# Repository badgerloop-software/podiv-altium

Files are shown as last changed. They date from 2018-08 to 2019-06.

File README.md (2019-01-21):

# podiv-altium
Altium repository for podiv. This project is set up to provide all documentation, design and data validation required for the Badgerloop Pod 4 PCBs.

## Prerequisites
Altium only works on Windows. See  [Altium System Requirements](https://www.altium.com/documentation/18.0/display/ADES/Altium+Designer+-+((System+Requirements))") for more information. An internet connection is required to connect to the license server and dual monitors are nice to ahve. Microsoft Excel is required for BOM generation.

## Installation
1. Contact Ethan Link or Ryan Castle to be added to the Badgerloop Team AltiumLive Account and the Badgerloop [Github](https://github.com/badgerloop-software"). You will receive an email from Altium with your account information. You may continue to step to step 8 without requiring an active license. If there is a delay for some reason, you can work on Altium training and practice on CAE computers or through [Citrix](https://remote.engr.wisc.edu/vpn/index.html), but we are usually able to add new users within 24 hours. CAE currently runs Altium 16, which has similar features but has a different interface and some bugs. Badgerloop currently supports Altium 19.0.10. 
2. Download the latest version of [Altium Designer](https://www.altium.com/products/downloads) 
3. Install Altium. Default file paths will work.
4. Insall [Git Bash](https://gitforwindows.org/") Git Bash (or whatever BASH emulation tool you are comfortable with)
5. Open Git Bash
6. Type the following commands into the command prompt window:
   + cd ../..
   + mkdir git
   + cd git
   + git clone https://github.com/badgerloop-software/podiv-altium.git
   + cd podiv-altium
   + git checkout -b <your-username_training>
   + Open Altium and sign in. You are now on a training branch that you will complete your first getting started project on if you are new to Altium. 
7. Go to User (Silhouette in the top right corner) -> License Management. Then Click Sign In and enter your username and password associated with Altium Live and accept the warning. It's also a good idea to check Sign me in when I start Altium Designer if you'd like to save a little time.

_NOTE: If you go click "Sign In" directly from User, you will be asked for a server address. This is not what you want. Go back to step 7 and hit License Management instead of Sign In._ 

8. Click Use to claim a license. If you are not using a valid license, you will be able to view files in Altium Designer but you will not be able to make edits. Ensure that you are choosing an Altium Designer License and not our PDN License. That's something else. 
9. You are now ready to use Altium. See [Training](#training) for more details on how to get started. 

## Training

+ View the [Badgerloop Altium Presentation](https://uwmadison.box.com/s/2sdt8kfaeyde04sg8edn62u7vtrdsiyx") for a getting started project. You can work locally for this project. Git-specific training will be posted at a later date. 
+ If you are new to using Git, read through the [Altium Git Guide](https://uwmadison.app.box.com/file/324684243638) which provides some common commands to get you started. 

## General Tips
+ Do not try to use Altium's built in check-out/commit tools. Instead, use Git from the terminal to perform git operations. This prevents a lot of conflicts. Learning how to use the command line is a really good thing to learn how to do as it's used in industry all over.
+ To save, CTRL + S may not save all of the files you are expecting it to. Instead, right click on the file you want to save and hit "save". Also, note that if a schematic document is edited, saving the entire project will only save the project structure, not the actual schematic file you have changed. 
+ Multiple libraries are used in part to reduce the number of conflicts between branches. It's important that you are regularly commiting and pushing your changes when multilpe users are working. Conflicts are possible to solve, but are somewhat challenging to do so. Libraries will be managed by Ryan Castle. Do not edit source libraries, instead, make changes in a temporary library.
+ Note that multilpe projects can reference the same libraries. Be careful if you are editing a component that has already been placed in another project, as even minor changes like pad size can have major unintended results. 

## Contributing
There are several ways to contribute to the repo. Check open issues to see what needs active work. Talk to the Avionics Lead or the Electrical Director about where your skill level can be most used.
+ Library components [TODO](https://github.com/badgerloop-software/podiv-altium/issues/16):

   + Schematic: Schematic libraries consist of the symbols used in schematics, as well as their pinoutsand link PCB and 3D components
   + PCB: PCB libraries consist of the footprints, pinouts and links to schematic symbols and 3D components. Footprints are the arrangement of pads and/or plated through-holes to physically attach and electrically connect a component to a printed circuit board. A silkscreen, keepout zone, and mechanical connections may also be added to a footprint
   + 3D Library: Each PCB footprint can be associated with a 3D STEP model and viewed in 3D mode of the PCB viewer. This is not required, but useful for exporting to the main pod MCAD as well as for enclosure design. 
+ Schematics:
   + Break out your datasheets! This is where the rubber meets the road of electrical engineering. Schematic design is where the highest level electrical engineering occurs, connecting different discrete components like resistors, capacitors, inductors and diodes to integrated circuits (ICs), connectors, hardware, etc. 
   + Schematic review: Look through an existing schematic and fill out the (still TODO) Schematic Review checklist. We want to catch issues as early as possible and correct before the board goes to layout or even worse, fabrication! 
+ PCBs:
   + I like to think of PCB layout as running through a maze several dozen times, where you control how the walls are constructed, there more more walls as you go along, and things can move as you go. PCB design is a learned skill, so the best thing to do is practice!
   + PCB review: Similar to schematic review, we want to find PCB layout issues before we send out to fabrication. Something as simple as a component flipped around can cause a boards unusable! 

## Directory Structure
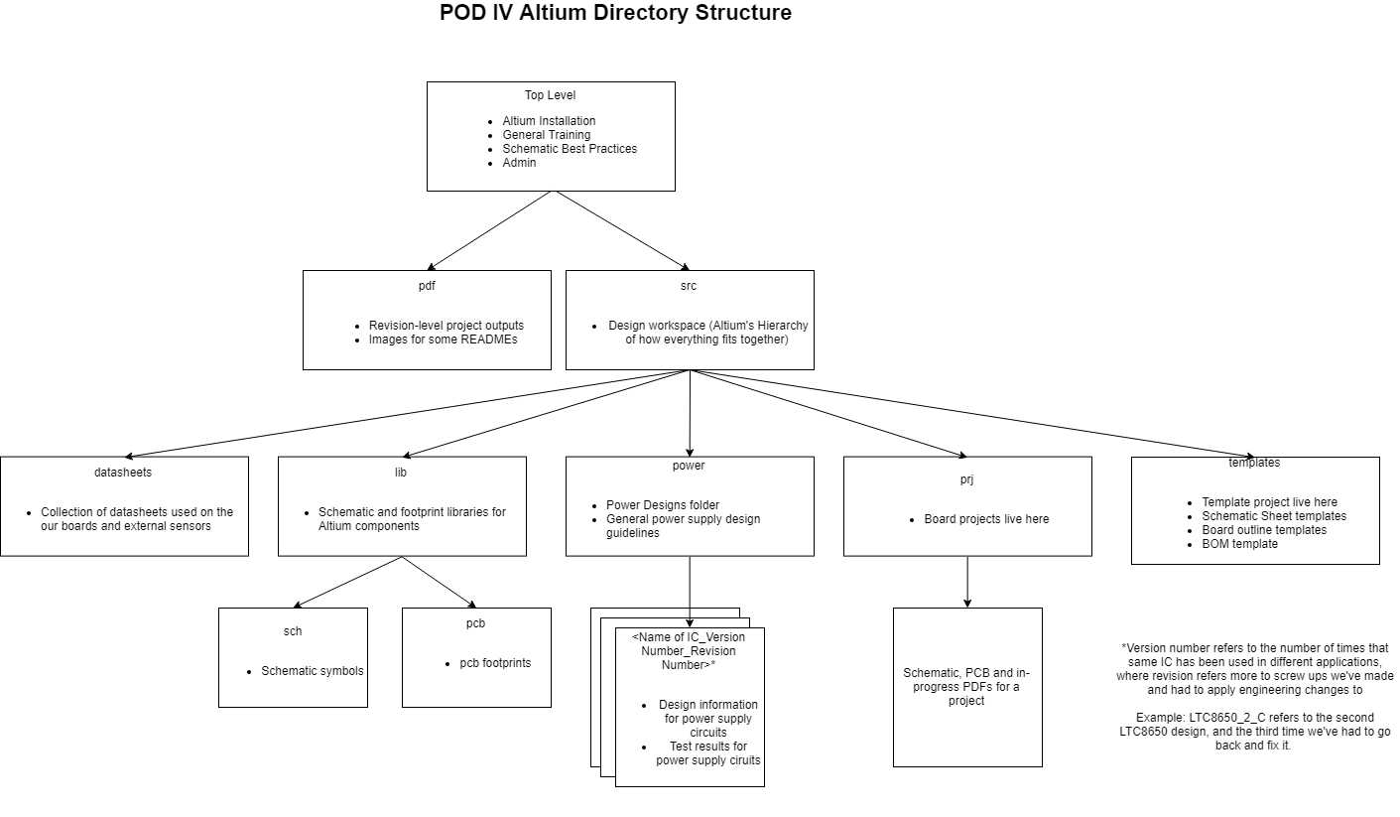
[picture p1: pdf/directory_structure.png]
Directory_Structure Directory Structure


## Contributors
+ [Ryan Castle](https://www.linkedin.com/in/ryan-castle-589721106/)
+ [Vaughn Kottler](https://www.linkedin.com/in/vaughnkottler/)
+ [Austin Muschott](https://www.linkedin.com/in/austin-muschott/)
+ [Tristan Steiner](https://www.linkedin.com/in/tristan-steiner-0bba76106/)

(Add yourself when you make your first commit!)

## Acknowledgements
+ [Altium](www.altium.com), for being an amazing sponsor! 
+ Dave Jones of the EEVBlog, as we'd have no idea what we were doing without his videos.

## Questions
If you have any questions, feel free to contact any contributor listed above on Slack (Badgerloop internal) or Linkedin (external)

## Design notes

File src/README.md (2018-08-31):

# Pod IV Multi-board PCB Project
The general approached for PCBs for Pod IV is to divide the workload into two types of boards-- processor boards and IO (Input/Output) boards. One processor board and one IO board will make up a module. The primary benefit to this approach is that the more complicated power and microcontroller circuitry can be done one time on the processor board, while module specific IO can be created to fit the specific module needs. 

## Module Notes:
+ Standard [connector](https://www.avnet.com/shop/emea/products/samtec/et60t-00-00-04-l-rt1-gp-3074457345629068722/") and pinout for each module allows for IO modules to be connected to any processor board safely
+ The blade connectors will be able to transfer the required current for up to 20 solenoids.
+ Must verify that signals routed over the longer leads are routed properly
+ Direct board <--> harness connection to eliminate module-box level wiring
+ I2C IO expanders used regularly as the standard interface between processor and IO boards. SPI and UART connections also routed to the connector but a NC (no connect) is acceptable.
+ 3D printed module boxes to fit the box to the boards, have holes pre-drilled

## Processor Board Notes:
+ 24V Input --> 5V, 3.3V outputs with reverse polarity protection, hold-up, surge stopper
+ Board mount processor with a QFN32 package utilized

## Module Board Notes:
+ Good project for beginners after you have completed the training board. 
+ Propoposed board ideas:
   + Navigation -- Accelerometer, Retroreflective sensor, distance sensor, wheel encoder
   + Pressure Vessel / Precharge PCB -- Pressure vessel monitoring and high voltage pre-charge circuit
   + Wireless communications -- replacement for the network access panel (NAP)
   + Braking -- IO for solenoids, pressure sensors
   + Low Voltage battery monitoring -- Battery management system for the low voltage system
   + Control Panel Display board -- Provide visual feedback for the system, useful for debugging.

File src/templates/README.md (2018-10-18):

# Templates
The purpose of this folder is to provide all templates for schematics sheets, PCBs, BOM, circuit snippets and reviews

## Circuit Snippets
[Badgerloop Altium Part II -- How to add a circuit snippet](https://www.youtube.com/watch?v=RExZlAXOayE&t=1s)

## Reviews
There are two templates associated with a review, the word document format and a powerpoint. The nominal workflow for a schematic or layout review are as follows:
1. The designer will output the following files and commit them to their working branch:
     * Schematic PDF
     * Board layout drawings, broken out layer by layer 
     * Gerbers, Drill Drawings
     * Pick and Place Files
     * BOM
     * Copy of the templates with the title < Project Name > _ Review _ < Rev > _ < Initial Date > copied into the podiv-altium/src folder
  
     * Note that there will be a template outputjob file that will take care of most of these outputs. 

2. The layout and/or schematic designer indicates that their board is ready for review by creating a new issue and assigning at least one peer reviewer or informing the electrical director they should assign a reviewer. 
3. Depending on the board complexity and timeline, we may want to have the board reviewed by a faculty member or one of our industry advisors. Work with the electrical director to arrange this. 
4. The reviewer will go through the review checklist. Note that the checklist is not exhaustive. Feel free to add rows and update the template. 
       * For short comments, quick calculations, design notes, etc., feel free to use the review word document. 
       * For more detailed comments or if screenshots are required, use the powerpoint format. Feel free to delete unused slides at the end of review. 
   
   Note that the slides will be listed as suggested reading for new PCB designers, as they will be a good record of mistakes we've made or almost made on our boards, in hopes that we won't do it again. 
5. The reviewer shall inform the designer of any changes required or suggested. We should also implement a way to indicate a change for the future revision, but not the current one. 
6. Any updates necessary should be made by the designer (nominally), but for some small changes it may be appropraite for changes to be made by the reviewer, just ensure that the RE knows and approves of the change.
7. Once a board is reviewed and okayed by all required parties, commenting on the git issue (or the designer / primary peer reviewer making a note of other's approval), output a final set of output files and add to the podiv-altium/pdf folder. It is critical that we have an exact copy of what we send to the board fabrication shop (and possibly assembly house) if we end up making future changes. 
8. Send files to the board shop. Work with them for any design for manufacturing (DFM) issues. 
9. Create a purchase order if necessary.
10. Wait 5-10 days and get your boards back.
11. Congratulations! You've just made a PCB with Badgerloop!

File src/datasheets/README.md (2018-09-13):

# Datasheets

Include datsheets for all components used on schematics and PCBs

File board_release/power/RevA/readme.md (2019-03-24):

# Power PCB BOM Changes
* Replace R8 with 0402 316K 1% Ohm resistor 
  * Adjust the 3.3V feedback resistor to output 3.3V instead of 5V
  * Yes, this does cause the "POS5V" net to output 3.3V and "POS3V3" to output 5V. This was the only way to spin the processor board in a couple of hours rather than a couple of days. 
* DNP U4
  * Individual Board sensing not going to be used, as overall information will come from ideal diode PCB

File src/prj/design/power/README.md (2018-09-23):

# Point of Load (POL) Power Supplies
## Getting Started
1. Watch the introductory [video](https://www.youtube.com/watch?v=o5OQcIHKOF0)
2. Download [Altium](www.altium.com) if you haven't already done so
3. Download [LTPowerCAD](http://www.analog.com/en/design-center/ltpowercad.html)
4. Download [Mathcad Express](https://www.ptc.com/en/products/mathcad-express-free-download/install)
5. Read some background information 
   * [Good Start](https://electronicsforu.com/resources/learn-electronics/smps-basics-switched-mode-power-supply)
   * [More Advanced](https://www.onsemi.com/pub/Collateral/SMPSRM-D.PDF)
6. Review the LTC8642S [datasheet](http://www.analog.com/media/en/technical-documentation/data-sheets/lt8642s.pdf)

## Board Power Tree

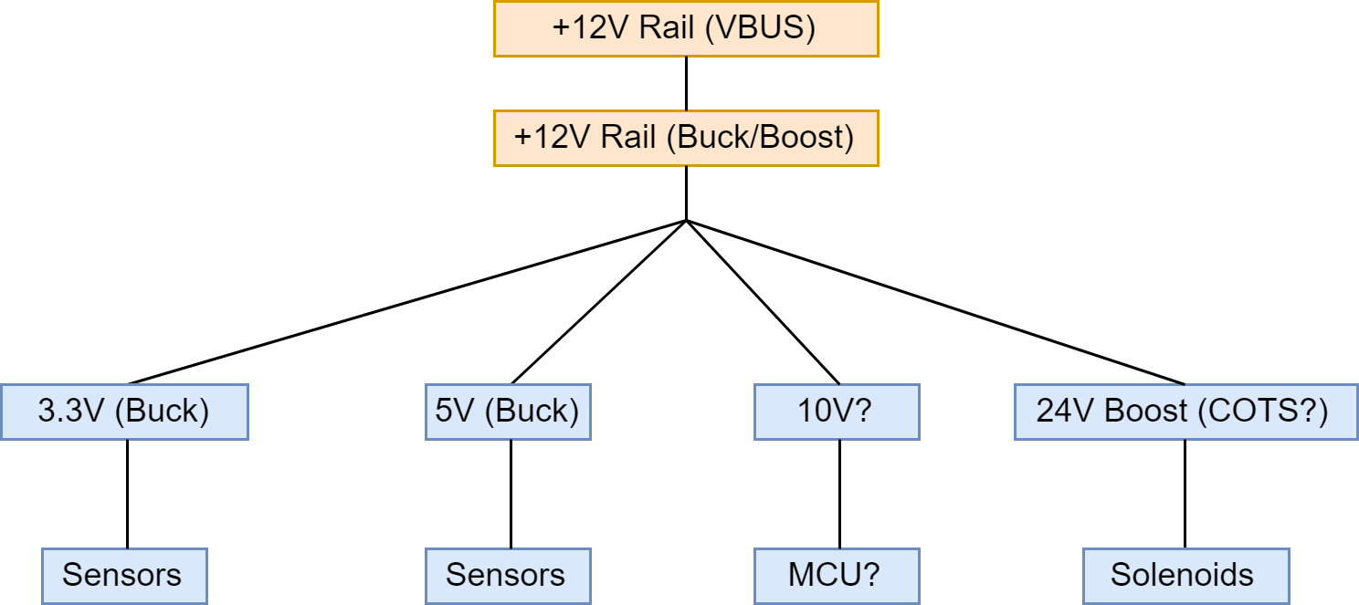
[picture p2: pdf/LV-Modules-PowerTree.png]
Power Tree


## Random Design Notes

* Use X7R for most capacitors, as these have better ratings over temperature. Note that this limits the range of nominal values you have access to per a given package size, but actual capacitance may be better over the range. 
   * Use C0G or NP0 Caps for compensation components if possible
* Feedback resistors should be 0.1% tolerance and Cff/Cfb should be X7R or NP0.
* Record all calculations in the mathcad files. Every component needs a justification.
* Estimating ESR and ESL is difficult. 
   * AVX published this [paper](https://www.avx.com/docs/techinfo/CeramicCapacitors/parasitc.pdf) for average ESL for package sizes. 
   * Depending on the manufacturer, ESR may be found on the component datasheet (Tayido Yuden) on a part specific search (TDK), Web app (Murata). It helps to do a search directly from the manufacturer's website. 
   * If you can't find data, you should probably use a different cap. If you really need to for some reason, you could copy characteristics from a similar component, but that's error prone.
* Capacitance changes with 
   * Temperature
   * Operating Frequency
   * DC Bias
   * Manufacturing tolerance
Be sure to account for all of these losses! Nominal capacitance doesn't really mean anything. Yes, you multilpy all of these losses together 
   * Example: 90% (temp losses)* 95% (Operating frequency) * 60% (DC Bias) * 80% (Manufacturing tolerance) = 41% of the datasheet capacitance value. That's like expecting 4.7uF and getting 2uF.
* Frequency Response simulations like those provided with LTPowerCAD can vary greatly if you put the incorrect inputs in for values like ESR and ESL. 
* Separate tantalum and ceramic capacitors for bulk and ceramic in PowerCAD. ESR is very different between the two and does not add like regular parallel resistance. 

## Testing Power Supplies

There are a number of design verification tests and measurements that should be performed for switch-mode-power-supplies or LDOs to ensure their operation in corner cases and over the lifetime of the product. This document will be updated with sample scope captures. 

Note that it is good practice to perform each test at min/max/nominal load cases, min/max/nominal input voltage, (min/max/nominal temperature is nice too but not required for our application)

### Steady-State Output Voltage Ripple
Measuring the peak-to-peak ripple current (on the order of 5mV/div on a scope). Looking for ESL spikes on the output as well. 

### Transient Response
How does a supply respond to a (near) instantaneous load. When current is drawn from the supply, the output voltage should drop, and then recover to the original output voltage minus load line losses. When the load is removed, the opposite should occur. You should be looking for a "critically damped", or single half-wave sinusoid, response as "ringing", or a fully sinusoidal wave with decreasing amplitude, indicates an unstable supply.
#### Testing Transient Response
Testing a transient response can be done in a number of ways. The most basic version is to manually connect and disconnect a power resistor to the output. 

Alternatively, more advanced forms of this test involve a device like an Intel [mini-slammer](https://designintools.intel.com/25A_Mini_Slammer_p/q6uj9a00ms25.htm_) or similar programmable load. Basically, you apply a waveform to the mini-slammer, which alters the effective load resistnace on the supply. This is an effective way to power on and power off a load at a regular frequency. Operation of a mini-slammer also requires an [Analog Discovery](https://store.digilentinc.com/analog-discovery-2-100msps-usb-oscilloscope-logic-analyzer-and-variable-power-supply/) or other wavegenerator and a mini-slammer [control board](https://designintools.intel.com/Mini_Slammer_Control_Board_p/q6uj9a00mscb.htm_)

Your oscilloscope should be set to NORMAL mode and trigger on your current-corresponding waveform. Scope captures should include Vin, Vout and load current. 
#### What do we get out of testing transient response? 
Testing the transient response of a supply gets you the following:
1. Evaluates stability of the supply (ringing present)
2. Measuring the deviation in output voltage from the norm. Some processors and FPGAs have 5% or even 3% output voltage tolerances.
3. Confidence that your supply will work when loads power on, relays engage, or there is some change in load.

### Vin / Enable / Vout / PGood Characteristics
Most power supplies that we are working with have a number of inputs and outputs that depend on one another. For example, for the LTC8640S supply topology, to have the normal operating output voltage, VIn must be above the Vin_min value listed in the datasheet, but the LTC8641S is in shutdown when the EN pin is low and active when the pin is high. According to the datasheet, When the LT8642S’s output voltage is within the ±8% window of the regulation point, the output voltage is considered good and the open-drain PG pin goes high impedance and is typically pulled high with an external resistor. We want to verify these signals do not glitch and characterize the delay between actions to ensure that we are not violating the minimum time thresholds in the datasheet. 

For these tests, set the oscilloscope to measure the following signals: Vin, EN, PGood, Output
#### Vin high with EN rising
Part A:
1. Hold Vin at the minimum operating voltage
2. Slowly increase the voltage on the ENABLE pin until the supply enables. Record this a EN_MIN
Part B:
1. Set your bench power supply to the expected operating minimum enable voltage
2. Enable the supply
3. The scope should be triggered ont he rising PGOOD channel.
4. Inspect the supply for any glitching of signals
5. Using the vertical cursors, measure the time between EN @ EN_MIN and the output reaching the steady state value and PGOOD going high. 
6. Repeat while the output is connected to a load.

#### Vin rising with EN high
Repeat the previous test except VIn will rise and EN will be held high

### Frequency Response Analysis
This guide will cover the basics of Frequency Response, but will focus on the practical aspects of frequency response. For more theory, check out these links
* [AN-1889 How to Measure the Loop Transfer Function of Power Supplies](http://www.ti.com/lit/an/snva364a/snva364a.pdf)
* [Ridley Engineering](http://www.ridleyengineering.com/design-center-ridley-engineering/)

According to Dr. Ridley, 
    "Loop gain is an essential measurement on all switching power supplies since it will provide information of stability, closed-loop performance, long-term ruggedness of the control, and a sensitive measure of many parts involved in the power supply construction."
This [article](http://www.ridleyengineering.com/design-center-ridley-engineering/41-frequency-response/104-026-frequency-response-measurement-part-4-loop-measurements.html) describes the industry standard technique for measuring loop response. Note that for the supplies we are working with the PWM controller and Switching Power Supply are integrated into the same IC. 

We are trying to measure the loop-gain and phase of the feedback system for the power supply. We purposely inject noise into the system at increasing frequency (Channel A) and measure the output (Channel B or R) and compare. R/A plots the gain and phase of the system. In short, we are trying to ensure that both gain and phase will not equal zero at the same time, which leads to an unstable transfer function. There are certain critical aspects of the system:
* Gain 0 dB crossover frequency: Where does the gain cross zero? Are there multilpe crossovers? This is also known as the "Bandwidth" of the supply. Rule of thumb is about 1/20th the switching frequency
* Phase Margin: What is the phase doing when gain is at zero? Depending on the application, anywhere from 30 degrees of margin (cheap toys) to > 70 degrees (helicopters, medical instruments) is required. For the pod, 50-60 degrees is the target. 
* Gain Margin: What is the gain doing when phase crosses zero? Rule of thumb, this should be less than -10 dB
It should be noted that these are just three points on an entire spectrum. Understanding different types of compensation networks and their gain and phase curves is a more advanced skill, but is still worthwhile. This [article](http://www.ridleyengineering.com/design-center-ridley-engineering/41-frequency-response/140-077-interpreting-loop-gain-measurements.html) goes into more detail. 

#### Why so much margin? 
Well, you think you're ok with 30 degrees of PM and -5dB of GM. But then it's a little chilly out one day and your iPhone stops working. Or it's a hot day in LA and we're getting in the tube and our boards turn off randomly. Or we've been using the supply for so long our caps start to lose some of their nominal value. Or 100 other things could change in the real world application of the circuit. Having sufficient margins allows for these changes. 

#### Why should we do this? 
More from Dr. Ridley:
   "The aerospace design world is probably the most rigorous in making complete sets of bode plots for input impedance, output impedance, audiosusceptibility, and loop gain. Outside of the aerospace world, it is less common to make this full set of measurements. Most experienced designers will make a loop gain measurement since they find that it is a very sensitive measure of just about everything in the power stage and the feedback path. **If some component is the wrong value, or something is built wrong, the loop gain is very likely to show that there is a problem.**"

#### How to perform the test
For now, I will just link to Dr. Ridley's explaination of the test. [AN_026](http://www.ridleyengineering.com/design-center-ridley-engineering/41-frequency-response/104-026-frequency-response-measurement-part-4-loop-measurements.html)

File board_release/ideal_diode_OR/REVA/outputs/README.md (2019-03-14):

* Ideal Diode PCB
    
     * Intended to be an efficient way to "Diode OR" multilpe batteries together in parallel. However, traditional diode OR'ing results in a relatively large power drop across the diodes. This design uses an LTC4359 Ideal Diode Controller with Reverse Input Protection. The controller drives external N-Channel MOSFETs to replace a traditional Schottky Diode

* Ideal Diode PCB Enclosure
    
     * PCB enclosure that contains the ideal diode PCB, 12V regulator and a 12-24V Boost converter
    
     * Mechanical enclosure is a relatively compact 3D printed enclosure. The primary system components are secured by heat set inserts.
 
    * Harnessing goes out to the D-SUB connectors on the outside of the box
.
         * This setup shows why we avoid routing to connectors mounted to the outside of boxes and we avoided internal box harnessing on our other PCB modules.

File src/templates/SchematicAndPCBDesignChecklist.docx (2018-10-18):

Badgerloop Schematic and PCB Design Review Checklist

Project:

RE:

Peer Reviewer 1:

Peer Reviewer 2:

Instructor Reviewer (Optional):

Industry Reviewer (Optional):

Link to Project:

Link to Schematic PDF:

Link to PCB Output:

Schematic Symbols

| Review | Comments
☐ ☐ | Does each component contain at the minimum: - Manufacturer - Manufacturer P/N - Digkey Link: - Description - Default Designator - Datasheet Link
☐ ☐ | Verify pin map is correct
☐ ☐ | Does the symbol represent the actual circuit? For example, a wheatstone bridge package could be represented as discrete resistors in a rectangle for ease of understanding the circuit. Op-Amps too!
☐ ☐ | Does the symbol align to the grid? Do pins align to gird?
☐ ☐ | Are symbols located in their appropriate library or does the project use the “Temp” library

Schematic

| Review | Comments
☐ ☐ | Inputs on left side, outputs on right side (where possible)
☐ ☐ | Schematic information distributed across sheets (i.e. is it easy to read? Is everything jammed onto one sheet?)
☐ ☐ | Title blocked filled in?
☐ ☐ | Are all components on grids? Are all components even spaced, aligned horizontally, vertically, where possible?
☐ ☐ | Are nets named appropriately?
☐ ☐ | Are comments used to inform design, pcb, or operation notes?
☐ ☐ | Is the sheet size 11.0/8.5”?
☐ ☐ | Are component prefixes appropriate? (R for resistor, C for capacitor) Are they numbered sequentially?
☐ ☐ | Minimize Diversity: fewer unique parts in the design is preferable for less manufacturing errors, lower BOM cost, and ease of purchasing.
☐ ☐ | Compile project and ensure that no components are no unwaived DRC. Check that no DRC flags are appropriate
☐ ☐ | Is there an LTSpice simulation of the circuit?
☐ ☐ | Are unused pins accessible for future use or debug?
☐ ☐ | Add pull-ups and pull-downs for pins. DNP the unused component.
☐ ☐ | Does your circuit behave predictably during startup?
☐ ☐ | Does sequencing of power supplies matter?
☐ ☐ | Do capacitors have a path to GND after power-down?
☐ ☐ | Do all power nets follow the convention 5V, 3V3, LV_Batt+, etc.?
☐ ☐ | Is the load at outputs within a safe range?
☐ ☐ | Are pull-up/pull down resistors sized appropriately?
☐ ☐ | Are power resistors sized appropriately?
☐ ☐ | Does your circuit include ESD protection?
☐ ☐ | Are address pins connected to (sometimes) DNP pull-up/pull-downs? Is there a comment for the expected address on the schematic
☐ ☐ | Do you have bypass capacitors on all ICs?

Design for Test

☐ ☐ | Is there a test plan for the board?
☐ ☐ | Is there a bring-up plan for the board?
☐ ☐ | Have you contacted PCB and assembly houses during design?
☐ ☐ | Is Hipot testing required?
☐ ☐ | Are there GND and power supply test points available?
☐ ☐ | Are there test pads on critical signals? (Some places recommend 80% of nets to have a test point!)
☐ ☐ | Breakout NC pins to DNP components
☐ ☐ | Are all nets named?
☐ ☐ | Have you defined Net classes? Especially for boards with high and low voltage, high speed, etc.
☐ ☐ | What test equipment is required for this board?

Reliability

☐ ☐ | Are transitor maximum rated voltage greater than Vnom / 0.80?
☐ ☐ | Are maximum rated voltage of capacitors (Vmax) greater than 200% of Vnom?
☐ ☐ | Is the power rating of resistors greater than Pnominal / 0.75?

PCB Layout

☐ ☐ | Are board outline, dimensions defined in a BOARD OUTLINE Layer?
☐ ☐ | Do you have proper mounting holes?
☐ ☐ | Are mount hole locations agreed upon with mechanical systems? (lock mount hole or other mechanical interfaces)
☐ ☐ | Are all devices on the top-side? (Optional, but greatly preferred)
☐ ☐ | Are components aligned? Are diodes and polarized capacitors positioned with their cathodes/poles pointing in the same direction?
☐ ☐ | Make sure all jumpers, LEDs, connectors, switches, displays, etc. are okayed by mechanical, ok with the system
☐ ☐ | Is pin 1 of connectors marked?
☐ ☐ | Is there enough clearance around all components?
☐ ☐ | Is all silkscreen set to Arial? Refdes should be set to 40mil
☐ ☐ | Is the badgerloop logo, board name, revision and designer in silkscreen? Doesn’t have to be large
☐ ☐ | Does the board have or need fiducials or tooling holes?

Routing

☐ ☐ | Are all traces rated for their expected current?
☐ ☐ | Avoid vias in pad where possible.
☐ ☐ | Follow keepout zones around screw heads
☐ ☐ | Keep 50mil from board edge.
☐ ☐ | Do your polygons have any “dead copper” or “bottlenecks”?
☐ ☐ | Do you have a GND plane, Power plane?
☐ ☐ | Are you using thermal reliefs?
☐ ☐ | Avoid routing directly between two adjacent SMD pads
☐ ☐ | Avoid <90 deg routing (Altium’s Acute Angle rule) to avoid acid traps

Other PCB

☐ ☐ | Is the silkscreen useful? Silk should help you with bringup of the board or operation. Label connectors, configuration jumpers, LED meaning, etc.
☐ ☐ | Does silkscreen overlap with pads?
☐ ☐ | Are your through-holes plated?
☐ ☐ | Did you consolidate your drill sizes?
☐ ☐ | Did you check with your manufacturer about “Slots” (rectangular holes sometimes used by connectors, components)
☐ ☐ | Did you generate the proper output drawings, gerbers, and drill drawings? CAM files are good too!
☐ ☐ | Did you run DRC?
☐ ☐ | Export as a .STEP file and send to mechanical for integration.

Bill of Materials

☐ ☐ | Are all your parts exported to the BOM?
☐ ☐ | Do you require any spare components?
☐ ☐ | Are there any components that are not on the BOM directly, but should be added (screws, standoffs, fuses, etc)
☐ ☐ | Do you have a link to all components (digikey)
☐ ☐ | Do another BOM consolidation Check
☐ ☐ | Are all components in stock?

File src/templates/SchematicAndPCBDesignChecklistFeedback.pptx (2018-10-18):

## Badgerloop Schematic and PCB Review Notes

<Project>
<RE>
<Reviewer 1 and 2>

## Schematic Symbol Feedback

## Schematic Feedback

## Design For Test Feedback

## Reliability Feedback

## Layout Feedback

## Routing and General PCB feedback

## BOM Feedback

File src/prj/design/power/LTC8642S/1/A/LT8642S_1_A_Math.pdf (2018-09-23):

# LT8642S_1_A Power Design

Parameters

Vinnom ≔13.2 V | Voutnom ≔5 V | Iout_min≔0 A
Vinmin≔10 V | Voutmax≔Voutnom ⋅ 1.05=5.25 V | Iout_max≔8 A
Vinmax≔15 V | Voutmin≔Voutnom ⋅ 0.95=4.75 V | Fsw≔1.6 MHz

Vpmax≔⎛⎝Voutmax-Voutnom

| ⎞ ⎠ ⋅ 0.25=0.063 V

FB Resistor Calcs
Rbot≔6.8
Rtop_calc≔Rbot⋅ | =

⎛
⎜

⎝―――-

Voutnom
0.597

### 1 V

⎞
⎟
⎠
50.151 V | Need to fix units. 50kOhms

Switching Frequency
Set Fsw
Rt≔ | =

⎛
⎜
⎝

――――-

| 46.5
⎛ | ⋅ ⎝Fsw

⎞

⎠ 10⁻⁶

### 1 s

⎞
⎟
⎠

28.063 s

Fsw OK?
Datasheet Values
Vsw_top≔0.2 V | Vsw_bot≔0.1 V | ton_min≔35 ns

Fsw_max_allowable≔―――――――――――=

⎛⎝Voutnom +Vsw_bot⎞
⎠
t | ⋅ on_min ⎛⎝Vinnom -Vsw_top+Vsw_bot⎞
⎠

⎛⎝1.112 ⋅ 10⁷ ⎞

⎠ ―1
s

Fsw_max_allowable>Fsw =1
Vinmin_allowable≔――――――- | + | =

⎛⎝Voutnom +Vsw_bot⎞
⎠
1-F ⋅ sw ton_min

Vsw_bot Vsw_top 5.503 V

Vinmin_allowable<Vinmin=1

Created with PTC Mathcad Express. See www.mathcad.com for more information.

Inductor Calculations

Linitial≔ | ⋅ | =

⎛
⎜
⎝

――――――

Voutnom +Vsw_bot

Fsw

⎞
⎟
⎠

0.5 ⎛⎝1.594 ⋅ 10⁻⁶⎞
⎠ Wb
ΔIL≔――――⋅ | | =

Voutnom

L ⋅ initial Fsw

⎛
⎜
⎝

1-―――

Voutnom
Vinmax

⎞
⎟
⎠

1.307 Iload_max_min≔13.5

Iload_max_max≔18
IL_peak_1≔Iload_max_min+0.5 ⋅ΔIL=14.154

IL_peak_2≔Iload_max_max+0.5 ⋅ΔIL=18.654

Input Caps | η≔0.9 | Estimated efficiency

Dmax≔――――=

Voutnom
Vinmax ⋅η

0.37

Extra 1000 is to convert
Cinmin≔――――――――――――= | MHz to KHz from Fsw I | ⋅ | ⋅ | ⋅ | ⋅ out_max Dmax

⎛⎝1- Dmax

⎞
⎠ 1000 1000

F ⋅ sw Vpmax

18.656 F
See http://www.ti.com/lit/an/slta055/slta055.pdf
equation 1, 9
Cinbulk≔―――――――――=
1.21 ⋅ I | ⋅ | ⋅ out_max Iout_max Linitial

Vpmax ⋅Vpmax

0.032 ―s ⋅――

### 4 A

3
kg ⋅m

2
Adjusting for units: 320uF

Design note: Vin should be bypassed with at least 3 ceramic caps: Two small 0402 or 0603 <1uF caps on either side and a larger 4.7uF cap (X7R)

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
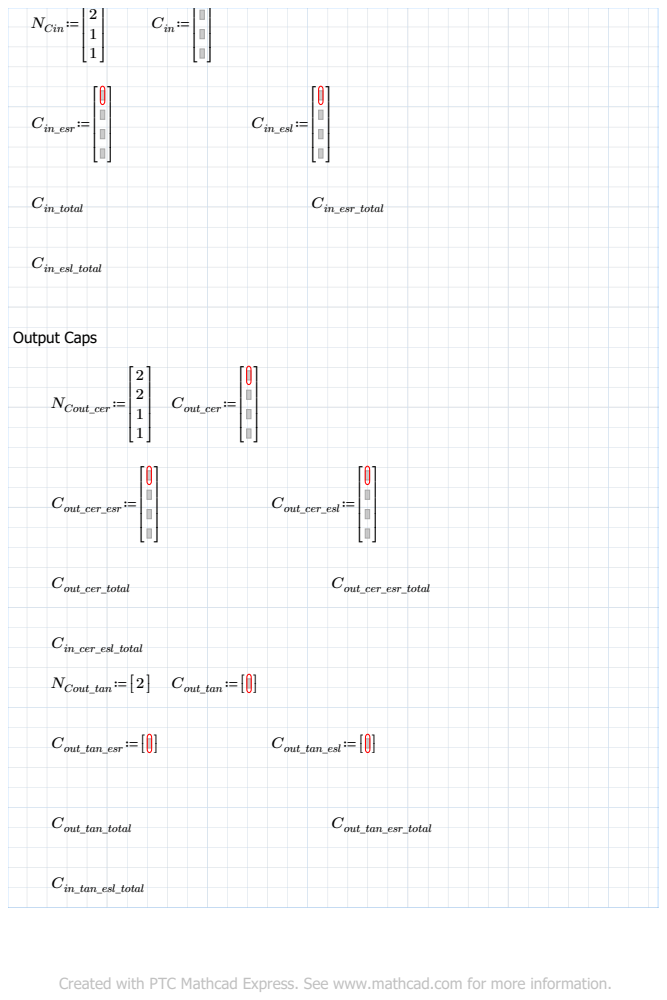
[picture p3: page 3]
NCin≔; Cin≔; Cin_esr≔; Cin_esl≔; Cin_total; Cin_esr_total; Cin_esl_total; Output Caps; NCout_cer≔; Cout_cer≔; Cout_cer_esr≔; Cout_cer_esl≔; Cout_cer_total; Cout_cer_esr_total; Cin_cer_esl_total; NCout_tan≔[; ] Cout_tan≔[ [; Cout_tan_esr≔[ [; Cout_tan_esl≔[; Cout_tan_total; Cout_tan_esr_total; Cin_tan_esl_total

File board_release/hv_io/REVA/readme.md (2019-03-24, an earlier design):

# Rework
* Latch global reset
  MCU_Latch to U8 connected to BMS_IMD_LATCH on U11 and PS_Latch on U10
Shutdown Circuit Input Switches
*  Input Connectors for Shutdown Circuits were not added ot board: Issue was resolved by connecting 18 awg wire to the underside of the PTH on the jumper to the PTH on the dsub.
     * Connector J4B:
     * Pin 13: Inertia Switch +
     * Pin 14: Inertia Switch -
     * Pin 17: Master/E-Stop Switch +
     * Pin 18: Master/ E-Stop Switch -
* Note: Issues will be resolved on REVB

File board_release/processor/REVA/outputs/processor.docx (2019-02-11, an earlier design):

# Introduction

This PCB serves as a breakout board for the Beaglebone, a power passthrough to the IO PCBs, CAN Circuitry and a generic LED indicator circuit. The PCB is known as the Device Under Test (DUT).

# Estimated Time

2 Hours per board

# Prerequisites

Attend the Badgerloop Soldering and PCB workshop or receive approval from an electrical lead. Some experience with solder paste dispensing or hand soldering SMD components is required.

# Required Equipment

- P4_LV_Processor_002_REVA PCBs (Qty up to 6) (DUT)
- Soldering iron
- Solder Paste
- Soldering Oven
- Solder
- Side cutters (snips)
- PCB BOM – SEE BOM FILE
- Microscope / Magnifying Glass / Calipers (optional)

# Visual Inspection

A simple visual inspection of the DUT includes:

1. Board thickness Design ______ Measured: _____
2. Board dimensions Design ______ Measured: _____
3. Warpage: Verified _____
4. Short circuit, bridge, open circuit, voids Verified _____
5. Surface quality (scratches, scrapes, burrs, etc.) Verified _____
6. Holes and Vias hole drilled, plating present Verified _____
7. Add a serial number to the DUT with permanent marker. Boards should be numbered with this format: <Abbreviated Name>-<Number>-<Revision> for example the first board would be labeled PBB-001-A for Processor BeagleBone, 001-006 for the unique identifier and A for the revision.

# Fit Check

1. Place the processor PCB into the LV and HV module boxes and secure the 4-40 screws.
2. Connect the power PCB
3. Connect the LV_IO and HV_IO PCBs
4. Place the assembled module into the 3D Printed case and secure the 4-40 screws.

# Soldering

## SMD Soldering

1. Apply solder paste to all populated SMD pads
  a. Note, if a component won’t be populated for whatever reason, do not apply solder paste. Bake boards soon after placement.
2. Place all SMD resistors (R1-R9, R16, R28-R31), capacitors (C1 – C7) LEDs (LED1-6), Diodes (D1-D2) and ICs (U1, U3-U6)
  a. I find it helpful to have a printout of the schematic and mark off when a component is placed on the board. This prevents DNP (Do Not Place) components from getting populated.
  b. Do not populate R10-R15, R17-27
  c. U2 is 0.1” headers. Do not put solder paste on through holes.
3. Bake boards following instructions for the specific oven.

### Soldering Inspection 1

1. Verify there are no shorts between adjacent solder joints. Using a magnifying glass or microscope is useful. Adjacent pins on the controllers need to be inspected carefully
2. Verify all solder joints have the appropriate amount of solder.
3. Heat up any un-melted solder paste with an iron if necessary.
4. Touch up any solder joints with an iron if necessary. Use hot air if you are trained with that tool.

## Through Hole Soldering

1. Insert the screw terminals U2 and solder one pin on each component. Ensure that the component is flush to the PCB. Reheat the solder joint and adjust the component if it is not flush. Then solder the other pins.
2. Insert the 0.1” headers in P1-P13 and solder. Ensure that the component is flush to the PCB. Reheat the solder joint and adjust the component if it is not flush. Then solder the other pins.
3. Insert J1 flush to the PCB. Solder one pin and ensure that the bottom of the connector touches the top of the PCB. Reheat the joint and slide the connector as necessary. It is critical that this component is flush. Then solder the rest of the pins.
4. Repeat for J2 and J3
5. Populate P1

### Soldering Inspection 2

1. Repeat the same steps as soldering Inspection 1

## Assembly

1. Connect the beaglebone black to the U2 0.1” headers.

# Testing

## Electrical Testing

### Continuity / Short Circuit Testing

1. Using a digital multimeter set to continuity mode, verify there are no shorts between pins. It’s useful to be on “beep mode”.
  a. My strategy is to hold the red multimeter lead on pin one, then contact all other pins. Then move the red multimeter lead to pin 2, then contact all other pins.
  b. Verified _____

### Processor Operation

#### BeagleBone Power

1. Connect the beaglebone to the network via Ethernet
2. Using a current limited power supply, connect power directly to P2.
3. Enable the power supply
4. Verify network connection with the beaglebone and verify any status indicator LEDs

### CAN Testing

1. Work with the controls team to develop a test procedure
2. Suggested approaches are to have two processor PCBs connected by a short CAN Cable through J1 and verify messages can be sent over the bus.
  a. If you’re having problems, check that you have proper 120 Ohm termination resistors on the ends of the bus.
  b. If a node is terminating, populated P1

### IO Expander Testing

1. Work with the controls team to develop a test procedure
2. Suggested approaches are to verify the device is receiving power, the use a logic analyzer on the I2C Breakout Header to verify signals are properly transmitting.

## Integration Testing

Integration testing involves testing the interfaces between the DUT and any other PCB, connector and mechanical enclosure the DUT will nominally interact with.

1. Verify the PCB mounts properly in the enclosure. Verified _____

## Thermal and Vacuum Testing

1. As time allows, perform thermal and vacuum testing. This test could be combined with current sense amplification testing. Use a thermal camera, focusing on the FETs and shunt resistors

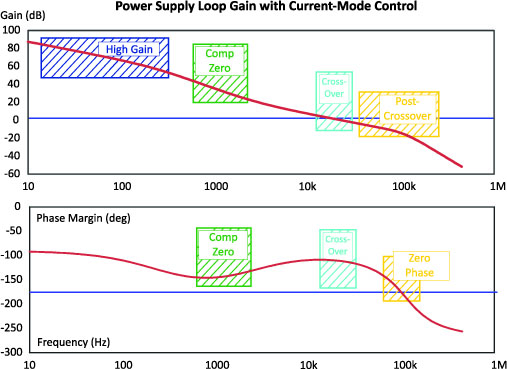
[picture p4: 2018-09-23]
src/prj/design/power/images/Fig_2.jpg

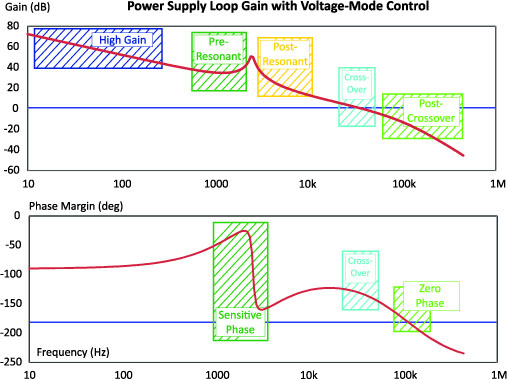
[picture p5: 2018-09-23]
src/prj/design/power/images/Fig_1.jpg

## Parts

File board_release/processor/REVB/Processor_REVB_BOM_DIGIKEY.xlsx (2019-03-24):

Index | Quantity | Part Number | Manufacturer Part Number | Description | Customer Reference | Available | Backorder | Unit Price | Extended Price USD
1 | 4 | AE10921-ND | A-DF 09 A/KG-T2S | CONN D-SUB RCPT 9POS R/A SOLDER |  | 4 | 0 | 0.77 | 3.08
2 | 4 | A32096-ND | 5747841-4 | CONN D-SUB PLUG 15POS R/A SOLDER |  | 4 | 0 | 3.6 | 14.40
3 | 4 | 1195-5053-ND | 09665527611 | CONN D-SUB RCPT 50POS R/A SOLDER |  | 4 | 0 | 15.88 | 63.52
4 | 1 | 235-1289-ND | SSCHNNN030PA2A3 | Honeywell pressure sensor |  | 1 | 0 | 10.86 | 10.86
5 | 1 | LTC6081IMS8#PBF-ND | LTC6081IMS8#PBF | IC OPAMP GP 3.5MHZ RRO 8MSOP |  | 1 | 0 | 4.31 | 4.31
6 | 10 | 490-11955-1-ND | GCD21BR71H104KA01L | CAP CER 0.1UF 50V X7R 0805 |  | 10 | 0 | 0.177 | 1.77
7 | 4 | 490-13420-1-ND | GCJ188R72A104KA01D | CAP CER 0.1UF 100V X7R 0603 |  | 4 | 0 | 0.28 | 1.12
8 | 4 | 490-4973-1-ND | GCM2165C1H472JA16D | CAP CER 4700PF 50V C0G/NP0 0805 |  | 4 | 0 | 0.64 | 2.56
9 | 100 | P120JCT-ND | ERJ-2GEJ121X | RES SMD 120 OHM 5% 1/10W 0402 |  | 100 | 0 | 0.0129 | 1.29
10 | 10 | P60.4LCT-ND | ERJ-2RKF60R4X | RES SMD 60.4 OHM 1% 1/10W 0402 |  | 10 | 0 | 0.046 | 0.46
11 | 10 | P1.96KLCT-ND | ERJ-2RKF1961X | RES SMD 1.96K OHM 1% 1/10W 0402 |  | 10 | 0 | 0.046 | 0.46
12 | 100 | P100KLCT-ND | ERJ-2RKF1003X | RES SMD 100K OHM 1% 1/10W 0402 |  | 100 | 0 | 0.0189 | 1.89
13 | 10 | P976KLCT-ND | ERJ-2RKF9763X | RES SMD 976K OHM 1% 1/10W 0402 |  | 10 | 0 | 0.046 | 0.46
14 | 100 | P10KJCT-ND | ERJ-2GEJ103X | RES SMD 10K OHM 5% 1/10W 0402 |  | 100 | 0 | 0.0129 | 1.29
15 | 50 | P0.0JCT-ND | ERJ-2GE0R00X | RES SMD 0 OHM JUMPER 1/10W 0402 |  | 50 | 0 | 0.0168 | 0.84
16 | 20 | P220CCT-ND | ERJ-6ENF2200V | RES SMD 220 OHM 1% 1/8W 0805 |  | 20 | 0 | 0.095 | 1.90
17 | 4 | MCP23017T-E/SOCT-ND | MCP23017T-E/SO | IC I/O EXPANDER I2C 16B 28SOIC |  | 4 | 0 | 1.24 | 4.96
18 | 4 | 296-30093-1-ND | SN65HVD256DR | IC TXRX CAN 5V HS 8SOIC |  | 4 | 0 | 2.22 | 8.88
19 | 10 | P34.0KLCT-ND | ERJ-2RKF3402X | RES SMD 34K OHM 1% 1/10W 0402 |  | 10 | 0 | 0.046 | 0.46
20 | 1 | ADR3433ARJZ-R7CT-ND | ADR3433ARJZ-R7 |  |  | 1 | 0 | 2.83 | 2.83
21 | 10 | 1276-6470-1-ND | CL21B105KBFNNNG | CAP CER 1UF 50V X7R 0805 |  | 10 | 0 | 0.102 | 1.02

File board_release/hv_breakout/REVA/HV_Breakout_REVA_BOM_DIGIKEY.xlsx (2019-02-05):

Index | Quantity | Part Number | Manufacturer Part Number | Description | Customer Reference | Available | Backorder | Unit Price | Extended Price USD
1 | 20 | 455-2249-ND | B4B-XH-A(LF)(SN) | CONN HEADER VERT 4POS 2.5MM |  | 20 | 0 | 0.194 | 3.88
2 | 6 | A32126-ND | 5747846-4 | CONN D-SUB RCPT 25POS R/A SOLDER |  | 6 | 0 | 4.43 | 26.58
3 | 6 | A32505-ND | 5-747912-2 | CONN D-SUB PLUG 25P STR SLDR CUP |  | 6 | 0 | 5.21 | 31.26
4 | 6 | A33668-ND | 5745134-1 | CONN BACKSHELL 25P 90/180DEG GRY |  | 6 | 0 | 5.4 | 32.40

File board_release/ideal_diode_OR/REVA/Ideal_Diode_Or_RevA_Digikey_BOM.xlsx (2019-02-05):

Index | Quantity | Part Number | Manufacturer Part Number | Description | Customer Reference | Available | Backorder | Unit Price | Extended Price USD
1 | 15 | 490-5610-1-ND | GCJ31BR72J472KXJ1L | CAP CER 4700PF 630V X7R 1206 | GCJ31BR72J472KXJ1L | 15 | 0 | 0.444 | 6.66
2 | 4 | SMAJ24ALFCT-ND | SMAJ24A | TVS DIODE 24V 38.9V DO214AC | SMAJ24A | 4 | 0 | 0.51 | 2.04
3 | 4 | SMAT70A-FDICT-ND | SMAT70A-13-F | TVS DIODE 70V 100V SMA | SMAT70A | 4 | 0 | 0.68 | 2.72
4 | 2 | 541-2626-1-ND | WSHM2818R0100FEA | RES 0.01 OHM 1% 7W 2818 | WSHM2818R0100FEA | 2 | 0 | 1.41 | 2.82
5 | 1 | 296-45088-1-ND | INA240A1PWR | IC AMP CURRENT SENSE 8-TSSOP | INA240X | 1 | 0 | 2.65 | 2.65
6 | 5 | LTC4359HMS8#TRPBFCT-ND | LTC4359HMS8#TRPBF | IC OR CTRLR N+1 8MSOP | LTC4359 | 5 | 0 | 6.92 | 34.60
7 | 6 | 497-15913-1-ND | STL90N6F7 | MOSFET N-CH 60V 90A F7 8PWRFLAT | STL90N6F7 | 6 | 0 | 2.3 | 13.80
8 | 2 | ED10562-ND | OSTVN03A150 | TERM BLK 3P SIDE ENT 2.54MM PCB | 3POS Screw Terminal | 2 | 0 | 1.07 | 2.14

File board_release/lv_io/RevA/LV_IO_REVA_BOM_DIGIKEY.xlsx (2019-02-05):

Index | Quantity | Part Number | Manufacturer Part Number | Description | Customer Reference | Available | Backorder | Unit Price | Extended Price USD
1 | 50 | P13571CT-ND | EZA-EG2A50AX | VARISTOR 0402 |  | 50 | 0 | 0.2924 | 14.62
2 | 2 | 1195-5057-ND | 09665627811 | CONN D-SUB PLUG 50POS R/A SOLDER |  | 2 | 0 | 17.3 | 34.60
3 | 25 | 160-1435-1-ND | LTST-C190KGKT | LED GREEN CLEAR CHIP SMD |  | 25 | 0 | 0.1488 | 3.72
4 | 4 | 1428-1123-1-ND | ICM-20948 | IMU ACCEL/GYRO/COMPI2C/SPI 24QFN |  | 4 | 0 | 8.04 | 32.16
5 | 4 | CAT24C32WI-GT3CT-ND | CAT24C32WI-GT3 | IC EEPROM 32K I2C 1MHZ 8SOIC |  | 4 | 0 | 0.2 | 0.80
6 | 4 | NCD9830DBR2GOSCT-ND | NCD9830DBR2G | IC ADC 8BIT 8CH I2C 16TSSOP |  | 4 | 0 | 2.7 | 10.80
7 | 12 | TPC817S1BRAGCT-ND | TPC817S1B RAG | OPTOISO 5KV TRANS 4SOP |  | 12 | 0 | 0.337 | 4.04
8 | 2 | MCP23017T-E/SOCT-ND | MCP23017T-E/SO | IC I/O EXPANDER I2C 16B 28SOIC |  | 2 | 0 | 1.24 | 2.48
9 | 4 | MCP9808-E/MS-ND | MCP9808-E/MS | SENSOR DIGITAL -40C-125C 8MSOP |  | 4 | 0 | 1.16 | 4.64
10 | 10 | 490-10502-1-ND | GRM21BC81E106KE51L | CAP CER 10UF 25V X6S 0805 |  | 10 | 0 | 0.294 | 2.94
11 | 16 | NHP220SFT3GOSCT-ND | NHP220SFT3G | DIODE GEN PURP 200V 2A SOD123FL |  | 16 | 0 | 0.32 | 5.12
12 | 250 | P0.0JCT-ND | ERJ-2GE0R00X | RES SMD 0 OHM JUMPER 1/10W 0402 |  | 250 | 0 | 0.00964 | 2.41
13 | 20 | P16033CT-ND | ERJ-P03J201V | RES SMD 200 OHM 5% 1/5W 0603 |  | 20 | 0 | 0.235 | 4.70
14 | 100 | P150JCT-ND | ERJ-2GEJ151X | RES SMD 150 OHM 5% 1/10W 0402 |  | 100 | 0 | 0.0129 | 1.29
15 | 100 | P100JCT-ND | ERJ-2GEJ101X | RES SMD 100 OHM 5% 1/10W 0402 |  | 100 | 0 | 0.0129 | 1.29
16 | 25 | 490-2472-1-ND | PRG18BB470MB1RB | PTC RESET FUSE 24V 29MA 0603 |  | 25 | 0 | 0.3948 | 9.87
17 | 16 | P16018CT-ND | ERJ-P03F1001V | RES SMD 1K OHM 1% 1/5W 0603 |  | 16 | 0 | 0.342 | 5.47
18 | 10 | P430KJCT-ND | ERJ-2GEJ434X | RES SMD 430K OHM 5% 1/10W 0402 |  | 10 | 0 | 0.031 | 0.31
19 | 100 | P680KJCT-ND | ERJ-2GEJ684X | RES SMD 680K OHM 5% 1/10W 0402 |  | 100 | 0 | 0.0129 | 1.29
20 | 20 | NTD3055L104T4GOSCT-ND | NTD3055L104T4G | MOSFET N-CH 60V 12A DPAK |  | 20 | 0 | 0.607 | 12.14
21 | 20 | 478-10855-1-ND | 12061C104KAT4A | CAP CER 0.1UF 100V X7R 1206 |  | 20 | 0 | 0.213 | 4.26
22 | 4 | 1125FFE-ND | 178-025-513R571 | CONN D-SUB RCPT 25POS R/A SLDR |  | 4 | 0 | 10.21 | 40.84
23 | 20 | 311-1523-1-ND | CC0603KRX7R0BB104 | CAP CER 0.1UF 100V X7R 0603 |  | 20 | 0 | 0.148 | 2.96
24 | 10 | 587-2394-1-ND | EMK212B7475KG-T | CAP CER 4.7UF 16V X7R 0805 |  | 10 | 0 | 0.198 | 1.98

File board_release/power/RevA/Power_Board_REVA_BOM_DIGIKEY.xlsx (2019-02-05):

Index | Quantity | Part Number | Manufacturer Part Number | Description | Customer Reference | Available | Backorder | Unit Price | Extended Price USD
1 | 8 | ZVN4106FCT-ND | ZVN4106FTA | MOSFET N-CH 60V 200MA SOT23-3 |  | 8 | 0 | 0.73 | 5.84
2 | 4 | A32121-ND | 5747845-4 | CONN D-SUB RCPT 15POS R/A SOLDER |  | 4 | 0 | 3.74 | 14.96
3 | 4 | AE10968-ND | A-DS 09 A/KG-T2S | CONN D-SUB PLUG 9POS R/A SOLDER |  | 4 | 0 | 0.77 | 3.08
4 | 10 | 160-1435-1-ND | LTST-C190KGKT | LED GREEN CLEAR CHIP SMD |  | 10 | 0 | 0.2 | 2.00
5 | 10 | 160-1436-1-ND | LTST-C190KRKT | LED RED CLEAR CHIP SMD |  | 10 | 0 | 0.2 | 2.00
6 | 5 | LT8650SEV#PBF-ND | LT8650SEV#PBF | IC REG BUCK DL 42V 5A SYNC 32LGA |  | 5 | 0 | 12.53 | 62.65
7 | 10 | 490-5797-1-ND | GCJ188R71E224KA12D | CAP CER 0.22UF 25V X7R 0603 |  | 10 | 0 | 0.228 | 2.28
8 | 10 | 490-7203-1-ND | GRM188R61E475KE11D | CAP CER 4.7UF 25V X5R 0603 |  | 10 | 0 | 0.258 | 2.58
9 | 16 | 490-5528-1-ND | GRM31CR61A476ME15L | CAP CER 47UF 10V X5R 1206 |  | 16 | 0 | 0.637 | 10.19
10 | 16 | 490-6042-1-ND | GCM155R71C473KA37D | CAP CER 0.047UF 16V X7R 0402 |  | 16 | 0 | 0.08 | 1.28
11 | 10 | 490-10751-1-ND | GRM21BR61H475KE51L | CAP CER 4.7UF 50V X5R 0805 |  | 10 | 0 | 0.256 | 2.56
12 | 10 | 490-11955-1-ND | GCD21BR71H104KA01L | CAP CER 0.1UF 50V X7R 0805 |  | 10 | 0 | 0.177 | 1.77
13 | 10 | 1N4148WTPMSCT-ND | 1N4148W-TP | DIODE GEN PURP 100V 150MA SOD123 |  | 10 | 0 | 0.131 | 1.31
14 | 100 | P15KJCT-ND | ERJ-2GEJ153X | RES SMD 15K OHM 5% 1/10W 0402 |  | 100 | 0 | 0.0129 | 1.29
15 | 100 | P100KJCT-ND | ERJ-2GEJ104X | RES SMD 100K OHM 5% 1/10W 0402 |  | 100 | 0 | 0.0129 | 1.29
16 | 10 | P191KLCT-ND | ERJ-2RKF1913X | RES SMD 191K OHM 1% 1/10W 0402 |  | 10 | 0 | 0.046 | 0.46
17 | 20 | P25.5CCT-ND | ERJ-6ENF25R5V | RES SMD 25.5 OHM 1% 1/8W 0805 |  | 20 | 0 | 0.081 | 1.62
18 | 10 | P56KJCT-ND | ERJ-2GEJ563X | RES SMD 56K OHM 5% 1/10W 0402 |  | 10 | 0 | 0.031 | 0.31
19 | 100 | P510KJCT-ND | ERJ-2GEJ514X | RES SMD 510K OHM 5% 1/10W 0402 |  | 100 | 0 | 0.0129 | 1.29
20 | 10 | P36.0KLCT-ND | ERJ-2RKF3602X | RES SMD 36K OHM 1% 1/10W 0402 |  | 10 | 0 | 0.046 | 0.46
21 | 4 | P0.01BVCT-ND | ERJ-8CWFR010V | RES 0.01 OHM 1% 1W 1206 |  | 4 | 0 | 0.71 | 2.84
22 | 100 | P750KACT-ND | ERJ-6GEYJ754V | RES SMD 750K OHM 5% 1/8W 0805 |  | 100 | 0 | 0.0249 | 2.49
23 | 10 | P270KACT-ND | ERJ-6GEYJ274V | RES SMD 270K OHM 5% 1/8W 0805 |  | 10 | 0 | 0.061 | 0.61
24 | 10 | SI4214DDY-T1-GE3CT-ND | SI4214DDY-T1-GE3 | MOSFET 2N-CH 30V 8.5A 8-SOIC |  | 10 | 0 | 0.694 | 6.94
25 | 12 | 1276-1860-1-ND | CL10A105KB8NNNC | CAP CER 1UF 50V X5R 0603 |  | 12 | 0 | 0.117 | 1.40
26 | 10 | 720-1376-1-ND | VJ0603Y103KXAAC | CAP CER 10000PF 50V X7R 0603 |  | 10 | 0 | 0.223 | 2.23
27 | 10 | 1276-2876-1-ND | CL31A106KBHNNNE | CAP CER 10UF 50V X5R 1206 |  | 10 | 0 | 0.477 | 4.77
28 | 5 | LTC4365CTS8#TRMPBFCT-ND | LTC4365CTS8#TRMPBF | IC OVERVOLTAGE PROT TSOT23-8 |  | 5 | 0 | 3.76 | 18.80
29 | 5 | ADR3433ARJZ-R7CT-ND | ADR3433ARJZ-R7 | IC VREF SERIES 3.3V SOT23-6 |  | 5 | 0 | 2.83 | 14.15
30 | 100 | P1.00MLCT-ND | ERJ-2RKF1004X | RES SMD 1M OHM 1% 1/10W 0402 |  | 100 | 0 | 0.0234 | 2.34
31 | 5 | 296-45091-1-ND | INA240A4PWR | IC AMP CURRENT SENSE 8-TSSOP |  | 5 | 0 | 2.65 | 13.25
32 | 12 | 1276-6470-1-ND | CL21B105KBFNNNG | CAP CER 1UF 50V X7R 0805 |  | 12 | 0 | 0.102 | 1.22
33 | 10 | 311-1136-1-ND | CC0805KRX7R9BB103 | CAP CER 10000PF 50V X7R 0805 |  | 10 | 0 | 0.08 | 0.80
34 | 100 | 490-6130-1-ND | GRM0335C1H4R7CA01D | CAP CER 4.7PF 50V C0G/NP0 0201 |  | 100 | 0 | 0.0068 | 0.68

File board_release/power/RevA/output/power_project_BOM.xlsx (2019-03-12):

Comment | Description | Designator | Footprint | LibRef | Quantity | Digi-Key Part Number | Manufacturer
1µF | CAP CER 1UF 50V X5R 0603 | C1, C11, C14, C? | SMD-0603C | GRM188R61H105KAALD | 7 | 490-10732-1-ND | Murata Electronics North America
10µF | CAP CER 10UF 50V X5R 1206 | C2, C4, C? | SMD-1206C | GRM31CR61H106KA12L | 6 | 490-5961-1-ND | Murata Electronics North America
1µF | CAP CER 1UF 50V X7R 0805 | C3, C5, C28, C? | SMD-0805C | GCJ21BR71H105KA01L | 7 | 490-10667-1-ND | Murata Electronics North America
0.22µF | CAP CER 0.22UF 25V X7R 0603 | C6, C7, C? | SMD-0603C | GCJ188R71E224KA12D | 6 | 490-5797-1-ND | Murata Electronics North America
4.7µF | CAP CER 4.7UF 25V X5R 0603 | C8, C15, C? | SMD-0603C | GRM188R61E475KE11D | 6 | 490-7203-1-ND | Murata Electronics North America
47µF | CAP CER 47UF 10V X5R 1206 | C9, C10, C16, C17, C? | SMD-1206C | GRM31CR61A476ME15L | 12 | 490-5528-1-ND | Murata Electronics North America
4.7pF | CAP CER 4.7PF 50V NP0 0603 | C12, C13, C? | SMD-0603C | GRM1885C1H4R7CA01D | 6 | 490-12722-1-ND | Murata Electronics North America
10000pF | CAP CER 10000PF 250V X7T 0805 | C16, C17, C18, C19, C20, C21, C25, C29 | SMD-0805C | GC321AD72E103KX01D | 8 | 490-13986-1-ND | Murata Electronics North America
0.047µF | CAP CER 0.047UF 16V X7R 0402 | C18, C19, C20, C21, C? | SMD-0402C | GCM155R71C473KA37D | 12 | 490-6042-1-ND | Murata Electronics North America
0.033µF | CAP CER 0.033UF 250V X7T 1206 | C22, C23, C26, C27 | SMD-1206C | GC331AD72E333KX01D | 4 | 490-13989-1-ND | Murata Electronics North America
10000pF | CAP CER 10000PF 25V X7R 0603 | C22, C23, C? | SMD-0603C | GRM188R71E103KA01D | 6 | 490-1520-1-ND | Murata Electronics North America
4.7µF | CAP CER 4.7UF 50V X5R 0805 | C24 | SMD-0805C | GRM21BR61H475KE51L | 1 | 490-10751-1-ND | Murata Electronics North America
220pF | CAP CER 220PF 50V NP0 0402 | C24, C28 | SMD-0402C | GCM1555C1H221JA16D | 2 | 490-4927-1-ND | Murata Electronics North America
22uF | CAP CER 10000PF 250V X7T 0805 | C25, C26 | SMD-0805C | GC321AD72E103KX01D | 2 | 445-11527-1-ND | TDK Corporation
0.10µF | CAP CER 0.1UF 50V X7R 0805 | C27, C29 | SMD-0805C | GCD21BR71H104KA01L | 2 | 490-11955-1-ND | Murata Electronics North America
10000pF | CAP CER 10000PF 50V X7R 0402 | C30 | SMD-0402C | GCM155R71H103KA55D | 1 | 490-4762-1-ND | Murata Electronics North America
CMJ2000 | DIODE CURRENT LIMITING SINGLE SM | CLD1, CLD2, CLD3 | SODFL350X80-2N | DIODE Current Limiting Single SM | 3 |  | Central Semiconductor Corp
Diode General Purpose | DIODE GEN PURP 100V 150MA SOD123 | D1 | Diode General Purpose | Diode General Purpose | 1 |  | Micro Commercial Co
N-MOS | MOSFET N-CH 60V 200MA SOT23-3 | FET1, FET2 | SOT95P240X110-3N | N-MOS Enhancement Mode | 2 |  | Zetex
D Connector 15 | Receptacle Assembly, 15 Position, Right Angle | J1 | DSUB1.385-2H15 | D Connector 15 | 1
D Connector 9 | Receptacle Assembly, 9 Position, Right Angle | J2 | DSUB1.385-2H9 | D Connector 9 | 1
IND 1.0uH 5.48x5.28x3.1mm 5mOhm ESR | XFL5030-102ME | L1, L2 | INDC5649X31N | IND 1.0uH 5.48x5.28x3.1mm 5mOhm ESR | 2
Inductor | Inductor | L2 | 0402-A | Inductor | 1
1uH | XFL5030-102ME | L? | IND_TAIYO_CBC201 | IND 1.0uH 5.48x5.28x3.1mm 5mOhm ESR | 4
GREEN 0603 |  | LED1, LED2 | LED 0603 GREEN | LED GREEN 0603 | 2 |  | Lite-On Inc.
LED RED 0603 | Red 631nm LED Indication - Discrete 2V 0603 (1608 Metric) | LED3 | LED 0603 RED | LED RED 0603 | 1 |  | Lite-On Inc.
LED GREEN 0603 |  | LED4, LED5 | LED 0603 GREEN | LED GREEN 0603 | 2 |  | Lite-On Inc.
#10 Mount Hole |  | MH1, MH2, MH3, MH4 | MH | #10 Mount Hole | 4
Header 3 | Header, 3-Pin | P1, P2, P3 | Pin Header 1x3 TH Pitch 2.54mm | Header 3 | 3
15k | RES SMD 15K OHM 5% 1/10W 0402 | R1 | SMD-0402-RES | ERJ-2GEJ153X | 1 | P15KJCT-ND | Panasonic Electronic Components
1M | RES SMD 1M OHM 1% 1/10W 0402, RES SMD 1M OHM 5% 1/10W 0402 | R2, R3, R4, R5, R6, R7, R14, R15, R16, R? | SMD-0402-RES | ERJ-2RKF1004X, ERJ-2GEJ105X | 25 | P1.00MLCT-ND, P1.0MJCT-ND | Panasonic Electronic Components
191k | RES SMD 191K OHM 1% 1/10W 0402 | R8, R9, R? | SMD-0402-RES | ERJ-2RKF1913X | 6 | P191KLCT-ND | Panasonic Electronic Components
25.5 | RES SMD 25.5 OHM 1% 1/8W 0805 | R10, R11 | SMD-0805-RES | ERJ-6ENF25R5V | 2 | P25.5CCT-ND | Panasonic Electronic Components
10k | RES SMD 10K OHM 5% 1/10W 0402 | R10, R15 | SMD-0402-RES | ERJ-2GEJ103X | 2 | P10KJCT-ND | Panasonic Electronic Components
0.0 | RES SMD 0.0OHM JUMPER 1/10W 0402 | R11, R12, R17, R18, R19, R20 | SMD-0402-RES | ERJ-2GE0R00X | 6 | P0.0JCT-ND | Panasonic Electronic Components
100k | RES SMD 100K OHM 5% 1/10W 0402 | R12, R13, R? | SMD-0402-RES | ERJ-2GEJ104X | 6 | P100KJCT-ND | Panasonic Electronic Components
0.22 | RES SMD 0.22 OHM 1% 1/6W 0402 | R13, R14 | SMD-0402-RES | ERJ-2BQFR22X | 2 | P.22AKCT-ND | Panasonic Electronic Components
24k | RES SMD 24K OHM 5% 1/10W 0402 | R16 | SMD-0402-RES | ERJ-2GEJ243X | 1 | P24KJCT-ND | Panasonic Electronic Components
56k | RES SMD 56K OHM 5% 1/10W 0402 | R17 | SMD-0402-RES | ERJ-2GEJ563X | 1 | P56KJCT-ND | Panasonic Electronic Components
510k | RES SMD 510K OHM 5% 1/10W 0402 | R18 | SMD-0402-RES | ERJ-2GEJ514X | 1 | P510KJCT-ND | Panasonic Electronic Components
36k | RES SMD 36K OHM 1% 1/10W 0402 | R21 | SMD-0402-RES | ERJ-2RKF3602X | 1 | P36.0KLCT-ND | Panasonic Electronic Components
0.01 | RES SMD 0.01 OHM 1% 1W 1206 | R22 | SMD-1206-RES | ERJ-8CWFR010V | 1 | P0.01BVCT-ND | Panasonic Electronic Components
750k | RES SMD 750K OHM 5% 1/8W 0805 | R23 | SMD-0805-RES | ERJ-6GEYJ754V | 1 | P750KACT-ND | Panasonic Electronic Components
270k | RES SMD 270K OHM 5% 1/8W 0805 | R24 | SMD-0805-RES | ERJ-6GEYJ274V | 1 | P270KACT-ND | Panasonic Electronic Components
10 | RES SMD 10 OHM 5% 1/10W 0402 | R? | SMD-0402-RES | ERJ-2GEJ100X | 4 | P10JCT-ND | Panasonic Electronic Components
TP |  | TP1, TP2, TP3, TP4, TP5, TP6, TP7, TP8, TP9, TP10, TP11, TP13 | Test Point | TP | 12
LT8650SEV#PBF | LT8650S - Dual Channel 4A, 42V, Synchronous Step-Down Silent Switcher 2 with 6.2ÂµA Quiescent Current | U1, U? | QFN50P600X400X103-32N240X440 | LT8650SEV#PBF | 4
LT8642S | 18V, 10A Synchronous Step-Down Silent Switcher 2 | U2 |  | LT8642S | 1
SI4214DDY-T1-GE3 | Mosfet Array 2 N-Channel (Dual) 30V 8.5A 3.1W Surface Mount 8-SO | U2 | SOIC-8_SI-L | SI4214DDY-T1-GE3 | 1
LTC4365CTS8#TRMP | Overvoltage, Undervoltage and Reverse Supply Protection Controller | U3 | TSOT-23_TS8 | LTC4365CTS8#TRMP | 1
INA240A | IC AMP CURRENT SENSE 8-TSSOP | U4 | SOIC127P600X175-8N | INA240A | 1 |  | TI
ADR3433 | IC VREF SERIES 3.3V SOT23-6 | U5 | SOT95P280X145-6N | ADR3433 | 1 |  | Analog Devices

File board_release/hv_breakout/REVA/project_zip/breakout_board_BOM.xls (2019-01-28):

Comment | Description | Designator | Digikey Link | Digikey P/N | Digi-Key Part Number | DNP | Footprint | LibRef | Quantity | Manufacturer | Manufacturer P/N
D Connector 25 | Receptacle Assembly, 25 Position, Right Angle | J1 |  |  |  |  | DSUB1.385-2H25A | D Connector 25 | 1
4-40 Mount Hole |  | MH, MH1, MH2, MH3 |  |  |  |  | MH | 4-40 Mount Hole | 4
JST-XH Header | JST-XH CONN HEADER VERT 4POS 2.5MM | P1, P2, P3, P4 | https://www.digikey.com/product-detail/en/jst-sales-america-inc/B4B-XH-A-LF-SN/455-2249-ND/1651047 | 455-2249-ND |  |  | JST - XH 4 Pos | JST-XH Header | 4 | JST Sales America | B4B-XH-A(LF)(SN)
Header 8 | Header, 8-Pin | P5 |  |  |  |  | Pin Header 1x8 TH Pitch 2.54mm | Header 8 | 1

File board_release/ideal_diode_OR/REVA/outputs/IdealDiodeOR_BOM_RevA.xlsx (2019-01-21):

Description | Designator | Digikey Link | Digikey P/N | Digi-Key Part Number | DNP | Footprint | LibRef | Quantity | Manufacturer | Manufacturer P/N | Comment
CAP CER 4700PF 630V X7R 1206 | C1, C2, C3, C4, C5, C6, C7, C8, C9, C10, C11, C12, C13 |  | 490-5610-1-ND |  |  | SMD-1206C | GCJ31BR72J472KXJ1L | 13 | Murata Electronics North America |  | 4700pF
TVS DIODE 24V 38.9V DO214AC | D1, D3, D5, D7 | https://www.digikey.com/product-detail/en/littelfuse-inc/SMAJ24A/SMAJ24ALFCT-ND/762500 | SMAJ24ALFCT-ND |  |  | INDM5026X18N | SMAJ24A | 4 | LittelFuse Inc | SMAJ24A | SMAJ24A
TVS DIODE 70V 100V SMA | D2, D4, D6, D8 | https://www.digikey.com/product-detail/en/diodes-incorporated/SMAT70A-13-F/SMAT70A-FDICT-ND/804910 | SMAT70A-FDICT-ND |  |  | SMAT70A | SMAT70A | 4 | Diodes Incorporated | SMAT70A-13-F | SMAT70A
 | MH1, MH2, MH3, MH4 |  |  |  |  | MH | 4-40 Mount Hole | 4 |  |  | 4-40 Mount Hole
Screw Terminal, 2-Pin | P1, P2, P3, P4, P5, P6, P7, P8 |  |  |  |  | 2POS TERM BLOCK | Screw Terminal 2x1 | 8 |  |  | Screw Terminal 2x1
Screw Terminal, 3-Pin | P9 |  |  |  |  | 3POS TERM BLOCK | Screw Terminal 3x1 | 1 |  |  | Screw Terminal 3x1
Header, 2-Pin | P10, P11, P12, P13 |  |  |  |  | Pin Header 1x2 TH Pitch 2.54mm | Header 2 | 4 |  |  | Header 2
 | PCB1 |  |  |  |  | PCB | PCB | 1 |  |  | .TITLE
MOSFET N-CH 60V 90A F7 8PWRFLAT | Q1, Q2, Q3, Q4 | https://www.digikey.com/product-detail/en/stmicroelectronics/STL90N6F7/497-15913-1-ND/5357115 | 497-15913-2-ND |  |  | DPAK228P991X238-4N | STL90N6F7 | 4 | 497-15913-2-ND | STL90N6F7 | STL90N6F7
RES 0.01 OHM 1% 7W 2818 | R1, R2 | https://www.digikey.com/product-detail/en/vishay-dale/WSHM2818R0100FEA/541-2626-1-ND/5419333 | 541-2626-1-ND |  |  | CAPMP7146X15N | WSHM2818R0100FEA | 2 | Vishay Dale | WSHM2818R0100FEA | WSHM2818R0100FEA
 | TP1, TP2, TP3, TP4, TP5, TP6, TP7, TP8, TP9, TP10, TP11, TP12 |  |  |  |  | Test Point | TP | 12 |  |  | TP
IC AMP CURRENT SENSE 8-TSSOP | U1 | https://www.digikey.com/product-detail/en/texas-instruments/INA240A1PWR/296-45088-1-ND/6562101 | 296-45088-1-ND |  |  | SOIC127P600X175-8N | INA240x | 1 | TI | INA240A1PWR | INA240x
IC OR CTRLR N+1 8MSOP | U2, U3, U4, U5 | https://www.digikey.com/product-detail/en/linear-technology-analog-devices/LTC4359HMS8-TRPBF/LTC4359HMS8-TRPBFCT-ND/8275335 | LTC4359HMS8#TRPBFCT-ND |  |  | 8SOP | LTC4359 | 4 | Analog Devices | LTC4359 | LTC4359

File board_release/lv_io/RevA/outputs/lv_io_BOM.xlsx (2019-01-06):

Bill of Materials
Source Data From: |  | lv_io_project.PrjPCB
Project: |  | lv_io_project.PrjPCB
Variant: |  | None
Creation Date: | 12/27/2018 | 10:42:49 AM
Print Date: | 2018-12-30 | 22:03:48
Production Quantity: | 1
Currency | <none>
Reference | Designator | Description | Manufacturer | #Column Name Error:Manufacturer Part Number | Quantity | Digikey P/N | #Column Name Error:Digikey Part Number
<Parameter Reference not found> | C1, C2, C3, C4, C5, C6, C7, C8 | CAP CER 0.1UF 100V X7R 0603 | Murata Electronics North America |  | 8
<Parameter Reference not found> | C9, C10, C19 | CAP CER 4.7UF 16V X7R 0805, CAP CER 4.7UF 6.3V X5R 0805 | Murata Electronics North America |  | 3
<Parameter Reference not found> | C11, C12 | C3216X7R2A105K160AM | TDK |  | 2
<Parameter Reference not found> | C29, C30, C31, C32 | CAP CER 10UF 25V X6S 0805 | Murata Electronics North America |  | 4
<Parameter Reference not found> | D1, D3, D5, D7, D9, D11 |  | Lite-On Inc. |  | 6 | 160-1435-1-ND
<Parameter Reference not found> | D2, D4, D6, D8, D10, D12 | ESD Supressor | EZAEG |  | 6 | P13571CT-ND
<Parameter Reference not found> | D13, D14, D15, D16, D17, D18, D19, D20, D21, D22, D23, D24, D25, D26, D27, D28 | ESD Supressor | EZAEG |  | 16 | P13571CT-ND
<Parameter Reference not found> | D29, D30, D31, D32, D33, D34, D35, D36 | DIODE GEN PURP 200V 2A SOD123FL | ON SEMI |  | 8 | NHP220SFT3GOSCT-ND
<Parameter Reference not found> | J1, J2 | Stacked DSub | Norcomp |  | 2 | 178-225FFE-ND
<Parameter Reference not found> | J5 | Receptacle Assembly, 9 Position, Right Angle |  |  | 1
<Parameter Reference not found> | J6 | Receptacle Header Assemby | HARTING |  | 1 | 1195-5057-ND
<Parameter Reference not found> | LED, LED1 |  | Lite-On Inc. |  | 2 | 160-1435-1-ND
<Parameter Reference not found> | MH1, MH2, MH3, MH4, MH5, MH6 |  |  |  | 6
<Parameter Reference not found> | P1 |  | Xsens |  | 1 | 512-MTI-3-DK
<Parameter Reference not found> | P2 | Header, 3-Pin |  |  | 1
<Parameter Reference not found> | P10 | Header, 3-Pin |  |  | 1
<Parameter Reference not found> | P21 | Header, 2-Pin |  |  | 1
<Parameter Reference not found> | Q1, Q2, Q3, Q4, Q5, Q6, Q7, Q8 | N-Channel Power MOSFET, 12 A, 60 V | ON SEMI |  | 8 | NTD3055L104T4GOSDKR-ND
<Parameter Reference not found> | R1, R2, R3, R4, R5, R6, R7, R8, R16, R17, R18, R19, R23, R24, R25, R26, R27, R29, R30, R31, R32, R33, R34, R35, R36, R45, R46, R47, R48, R49, R50, R51, R52, R59, R60, R61, R62, R64, R66, R67, R69, R75, R76, R80, R81, R97, R98, R99, R100, R101, R102, R103, R104, R113, R114, R115, R116, R117, R118, R119, R120, R121, R122, R169, R170, R171, R172, R173, R174, R175, R176, R177, R178, R179, R180, R181, R182, R183, R184 | RES SMD 0.0OHM JUMPER 1/10W 0402 | Panasonic Electronic Components |  | 79
<Parameter Reference not found> | R9, R12, R15, R20, R21, R22, R28, R78, R83, R86, R89, R92, R95, R105, R106, R107, R108, R109, R110, R111, R112 | RES SMD 10K OHM 1% 1/5W 0402, RES SMD 10K OHM 5% 1/10W 0402, RES SMD 10K OHM 0.5% 1/16W 0402 | Panasonic Electronic Components |  | 21
<Parameter Reference not found> | R10, R11, R79, R84, R87, R90, R93, R96 | RES SMD 200 OHM 5% 1/5W 0603 | Panasonic Electronic Components |  | 8
<Parameter Reference not found> | R13, R14, R41, R42, R43, R44, R57, R58 | RES SMD 150 OHM 5% 1/10W 0402 | Panasonic Electronic Components |  | 8
<Parameter Reference not found> | R37, R38, R39, R40, R53, R54, R55, R56 | RES SMD 100 OHM 5% 1/10W 0402 | Panasonic Electronic Components |  | 8
<Parameter Reference not found> | R63, R65, R68, R70, R71, R72, R73, R74 | PTC RESET FUSE 6V 330MA 0603 | Murata |  | 8
<Parameter Reference not found> | R77, R82, R85, R88, R91, R94 | RES SMD 1K OHM 1% 1/5W 0603 | Panasonic Electronic Components |  | 6
<Parameter Reference not found> | R161, R162, R163, R164 | RES SMD 430K OHM 5% 1/10W 0402 | Panasonic Electronic Components |  | 4
<Parameter Reference not found> | R165, R166, R167, R168 | RES SMD 680K OHM 5% 1/10W 0402 | Panasonic Electronic Components |  | 4
<Parameter Reference not found> | TP1, TP2, TP3, TP4, TP5, TP8, TP9 |  |  |  | 7
<Parameter Reference not found> | U1, U2 | IMU ACCEL/GYRO/COMPI2C/SPI 24QFN | TDK InvenSense |  | 2 | 1428-1123-1-ND
<Parameter Reference not found> | U3 | IC EEPROM 32K I2C 1MHZ 8SOIC | ON Semi |  | 1 | CAT24C32WI-Gt3CT-ND
<Parameter Reference not found> | U4 | IC ADC 8BIT 8CH I2C 16TSSOP | ON Semiconductor |  | 1 | NCD9830DBR2GOSCT-ND
<Parameter Reference not found> | U5, U6, U7, U8, U9, U10 | OPTOISO 5KV TRANS 4SOP | Taiwan Semi |  | 6 | TPC817S1BRAGCT-ND
<Parameter Reference not found> | U11 | IC I/O EXPANDER I2C 16B 28SOIC | Microchip |  | 1 | MCP23017T-E/SOCT-ND
<Parameter Reference not found> | U12, U13 |  |  |  | 2 | MCP9808-E/MS-ND
 |  |  |  |  | 243
Approved |  | Notes

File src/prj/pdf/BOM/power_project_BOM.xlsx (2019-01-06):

Bill of Materials
Source Data From: |  | power_project.PrjPCB
Project: |  | power_project.PrjPCB
Variant: |  | None
Creation Date: | 12/30/2018 | 9:48:17 PM
Print Date: | 2018-12-30 | 22:03:48
Production Quantity: | 1
Currency | <none>
Reference | Designator | Description | Manufacturer | #Column Name Error:Manufacturer Part Number | Quantity | #Column Name Error:Digikey P/N | #Column Name Error:Digikey Part Number
<Parameter Reference not found> | C1, C11, C14 | CAP CER 1UF 50V X5R 0603 | Murata Electronics North America |  | 3 | GRM188R61H105KAALD
<Parameter Reference not found> | C2, C4 | CAP CER 10UF 50V X5R 1206 | Murata Electronics North America |  | 2 | GRM31CR61H106KA12L
<Parameter Reference not found> | C3, C5, C28 | CAP CER 1UF 50V X7R 0805 | Murata Electronics North America |  | 3 | GCJ21BR71H105KA01L
<Parameter Reference not found> | C6, C7 | CAP CER 0.22UF 25V X7R 0603 | Murata Electronics North America |  | 2 | GCJ188R71E224KA12D
<Parameter Reference not found> | C8, C15 | CAP CER 4.7UF 25V X5R 0603 | Murata Electronics North America |  | 2 | GRM188R61E475KE11D
<Parameter Reference not found> | C9, C10, C16, C17 | CAP CER 47UF 10V X5R 1206 | Murata Electronics North America |  | 4 | GRM31CR61A476ME15L
<Parameter Reference not found> | C12, C13 | CAP CER 4.7PF 50V NP0 0603 | Murata Electronics North America |  | 2 | GRM1885C1H4R7CA01D
<Parameter Reference not found> | C18, C19, C20, C21 | CAP CER 0.047UF 16V X7R 0402 | Murata Electronics North America |  | 4 | GCM155R71C473KA37D
<Parameter Reference not found> | C22, C23 | CAP CER 10000PF 25V X7R 0603 | Murata Electronics North America |  | 2 | GRM188R71E103KA01D
<Parameter Reference not found> | C24 | CAP CER 4.7UF 50V X5R 0805 | Murata Electronics North America |  | 1 | GRM21BR61H475KE51L
<Parameter Reference not found> | C25, C26 | CAP CER 10000PF 250V X7T 0805 | TDK Corporation |  | 2 | GC321AD72E103KX01D
<Parameter Reference not found> | C27, C29 | CAP CER 0.1UF 50V X7R 0805 | Murata Electronics North America |  | 2 | GCD21BR71H104KA01L
<Parameter Reference not found> | CLD1, CLD2, CLD3 | DIODE CURRENT LIMITING SINGLE SM | Central Semiconductor Corp |  | 3 | DNP
<Parameter Reference not found> | D1 | DIODE GEN PURP 100V 150MA SOD123 | Micro Commercial Co |  | 1 | 1N4148WTPMSTR-ND
<Parameter Reference not found> | FET1, FET2 | MOSFET N-CH 60V 200MA SOT23-3 | Zetex |  | 2 | ZVN4106FCT-ND
<Parameter Reference not found> | J1 | Receptacle Assembly, 15 Position, Right Angle |  |  | 1 | A32121-ND
<Parameter Reference not found> | J2 | Receptacle Assembly, 9 Position, Right Angle |  |  | 1 | AE10968-ND
<Parameter Reference not found> | L1, L2 | XFL5030-102ME |  |  | 2 | XFL5030-102ME
<Parameter Reference not found> | LED1, LED2, LED4, LED5 | 160-1435-1-ND | Lite-On Inc. |  | 2 | 160-1435-1-ND
<Parameter Reference not found> | LED3 | Red 631nm LED Indication - Discrete 2V 0603 (1608 Metric) | Lite-On Inc. |  | 1 | 160-1436-1-ND
<Parameter Reference not found> | MH1, MH2, MH3, MH4 |  |  |  | 4 | DNP
<Parameter Reference not found> | P1, P2, P3 | Header, 3-Pin |  |  | 3 | DNP
<Parameter Reference not found> | R1 | RES SMD 15K OHM 5% 1/10W 0402 | Panasonic Electronic Components |  | 1 | ERJ-2GEJ153X
<Parameter Reference not found> | R2, R3, R4, R5, R6, R7, R14, R15, R16 | RES SMD 1M OHM 1% 1/10W 0402, RES SMD 1M OHM 5% 1/10W 0402 | Panasonic Electronic Components |  | 9 | ERJ-2RKF1004X, ERJ-2GEJ105X
<Parameter Reference not found> | R8, R9 | RES SMD 191K OHM 1% 1/10W 0402 | Panasonic Electronic Components |  | 2 | ERJ-2RKF1913X
<Parameter Reference not found> | R10, R11 | RES SMD 25.5 OHM 1% 1/8W 0805 | Panasonic Electronic Components |  | 5 | ERJ-6ENF25R5V
<Parameter Reference not found> | R12, R13 | RES SMD 100K OHM 5% 1/10W 0402 | Panasonic Electronic Components |  | 2 | ERJ-2GEJ104X
<Parameter Reference not found> | R17 | RES SMD 56K OHM 5% 1/10W 0402 | Panasonic Electronic Components |  | 1 | ERJ-2GEJ563X
<Parameter Reference not found> | R18 | RES SMD 510K OHM 5% 1/10W 0402 | Panasonic Electronic Components |  | 1 | ERJ-2GEJ514X
<Parameter Reference not found> | R19, R20 | RES SMD 0.0OHM JUMPER 1/10W 0402 | Panasonic Electronic Components |  | 2 | ERJ-2GE0R00X
<Parameter Reference not found> | R21 | RES SMD 36K OHM 1% 1/10W 0402 | Panasonic Electronic Components |  | 1 | ERJ-2RKF3602X
<Parameter Reference not found> | R22 | RES SMD 0.01 OHM 1% 1W 1206 | Panasonic Electronic Components |  | 1 | ERJ-8CWFR010V
<Parameter Reference not found> | R23 | RES SMD 750K OHM 5% 1/8W 0805 | Panasonic Electronic Components |  | 1 | ERJ-6GEYJ754V
<Parameter Reference not found> | R24 | RES SMD 270K OHM 5% 1/8W 0805 | Panasonic Electronic Components |  | 1 | ERJ-6GEYJ274V
<Parameter Reference not found> | TP1, TP2, TP3, TP4, TP5, TP6, TP7, TP8, TP9, TP10, TP11, TP13 |  |  |  | 12 | DNP
<Parameter Reference not found> | U1 | LT8650S - Dual Channel 4A, 42V, Synchronous Step-Down Silent Switcher 2 with 6.2ÂµA Quiescent Current |  |  | 1 | LT8650SEV#PBF
<Parameter Reference not found> | U2 | Mosfet Array 2 N-Channel (Dual) 30V 8.5A 3.1W Surface Mount 8-SO |  |  | 1 | SI4214DDY-T1-GE3
<Parameter Reference not found> | U3 | Overvoltage,Undervoltage and ReverseSupply Protection Controller |  |  | 1 | LTC4365CTS8#TRMP
<Parameter Reference not found> | U4 | IC AMP CURRENT SENSE 8-TSSOP | TI |  | 1 | INA240A
<Parameter Reference not found> | U5 | IC VREF SERIES 3.3V SOT23-6 | Analog Devices |  | 1 | ADR3433
 |  |  |  |  | 93
Approved |  | Notes

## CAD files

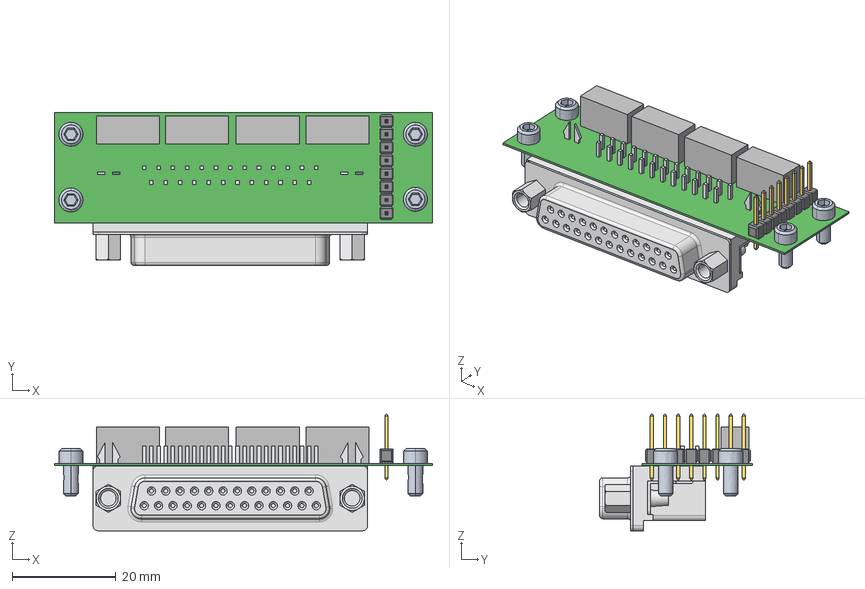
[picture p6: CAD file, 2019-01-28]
board_release/hv_breakout/REVA/project_zip/hv_breakout.step
73.0 x 29.5 x 22.5 mm
User_Library-d-sub25_connector
Extruded x 4
4_40_Screw x 4

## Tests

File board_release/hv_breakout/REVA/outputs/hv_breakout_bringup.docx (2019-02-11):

# Introduction

The battery breakout PCB is designed to connect to the voltage taps of each LiFePO4 battery. The PCB is mounted to the 3D printed battery enclosure. This is the smallest and simplest board currently on the pod. The PCB is known as the Device Under Test (DUT).

# Estimated Time

10 minutes per board

# Prerequisites

Attend the Badgerloop Soldering and PCB workshop or receive approval from an electrical lead. This board is all through-hole components, so only basic soldering is required. It is critical that all solder joints provide a solid electrical and mechanical connection.

# Required Equipment

- P4_HV_Breakout_001_REVA PCBs (Qty up to 6) (DUT)
- Soldering iron (this can be done with the Hanko Station in MEHQ)
- Solder
- Side cutters (snips)
- PCB BOM
  - Right angle, 25-pin DSUB connector (1 per board)
  - JST-XH connectors (4 per board)
  - 4-40 Screws, 4-40 Washers
  - 8-pin 0.1” header (note, this can be cut from a longer 0.1” header using side cutters)
- Microscope / Magnifying Glass / Calipers (optional)

# Visual Inspection

A simple visual inspection of the DUT includes:

1. Board thickness Design ______ Measured: _____
2. Board dimensions Design ______ Measured: _____
3. Warpage: Verified _____
4. Short circuit, bridge, open circuit, voids Verified _____
5. Surface quality (scratches, scrapes, burrs, etc.) Verified _____
6. Holes and Vias hole drilled, plating present Verified _____
7. Add a serial number to the DUT with permanent marker. Boards should be numbered with this format: <Abbreviated Name>-<Number>-<Revision> for example the first board would be labeled BOB-001-A for Breakout Board, 001-006 for the unique identifier and A for the revision.

# Fit Check

This DUT contains components with unverified component footprints. It’s good practice to verify major components fit in the DUT before soldering down components.

1. Verify fit for the right-angle dsub into J1 Verified _____
2. Verify fit for the JST-XH connectors into P1-P4 Verified _____
3. Verify fit for the 8-pin 0.1” header Verified _____

# Soldering

1. Power on the soldering iron and wait until the output light turns on.
2. Remove J1 (if present) as its standard to solder on the smallest components first. Insert the JST-XH connectors into P1-P4
3. Snip excess leads from the connector (leaving ~2mm exposed on the underside of the board)
4. Place the tip of the soldering iron on pin 1 of P1 and apply solder.
5. Ensure that the JST connector stays flush to the board. If it’s not, if you only have pin 1 soldered, you can reheat the joint and adjust the position. It’s much more difficult to heat up multiple joints at the same time if a component needs to be adjusted.
6. Apply solder to pin 3 of P1, then pin 2, then pin 4.
  a. It’s useful to apply solder to every other pin, reducing the likelihood of melting a the connectors
7. Repeat steps 2-6 for P2-P4
8. Insert J1. Snip excess leads from the connector (leaving ~2mm exposed on the underside of the board)
9. Solder pin 1 and pin 25. Ensure the connector is flush to the PCB. Reheat and adjust as necessary.
10. Insert J5 and solder pin 1. Verify the component is flush to the PCB.
11. Solder pin 8. Then solder pins 2, 4, 6, 3, 5, 7.

### Soldering Inspection

1. Verify there are no shorts between adjacent solder joints
2. Verify all solder joints have the appropriate amount of solder.

# Testing

This board is relatively simple, so the electrical testing is relatively short. For other PCBs, the electrical testing section will be more in-depth

## Electrical Testing

1. Using a digital multimeter set to continuity mode, verify there are no shorts between pins. It’s useful to be on “beep mode”.
  a. My strategy is to hold the red multimeter lead on pin one, then contact all other pins. Then move the red multimeter lead to pin 2, then contact all other pins.
  b. Verified _____

## Integration testing

Integration testing involves testing the interfaces between the DUT and any other PCB, connector and mechanical enclosure the DUT will nominally interact with.

1. Verify the voltage taps from the batteries connect to the P1-P4 Verified _____
2. Verify the proper mating connector for J1 fits. Verified _____
  a. Perform a continuity check between the JST and the solder cup on the mating connector.
3. Insert the DUT into the 3D printed enclosure and verify mechanical fit Verified _____

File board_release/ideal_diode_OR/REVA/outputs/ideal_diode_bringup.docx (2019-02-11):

# Introduction

The ideal diode board is a battery management PCB that parallels the batteries together and provides reverse polarity protection and reverse current protection without the large voltage drop and power loss experienced by a real diode. The PCB is known as the Device Under Test (DUT).

# Estimated Time

30 minutes per board

# Prerequisites

Attend the Badgerloop Soldering and PCB workshop or receive approval from an electrical lead. Some experience with solder paste dispensing or hand soldering SMD components is preferred.

# Required Equipment

- P4_LV_IdealDiode_001_REVA PCBs (Qty up to 2) (DUT)
- Soldering iron (this can be done with the Hanko Station in MEHQ)
- Solder
- Side cutters (snips)
- PCB BOM (Qty per board)
  - SMD Components
    - SMAJ24A Diode (QTY 4)
    - SMAT7 Diode (QTY 4)
    - STL90N6F7 (QTY 4)
    - LTC4359 Ideal Diode Controller (QTY 4)
    - INA240x Amplifier (QTY 1)
    - 4700pF CAP (QTY 12)
    - 10mOhm RES (QTY2)
  - Through-hole Components
    - 2-pin screw terminal (QTY 8)
    - 3-pin screw terminal (QTY 1)
    - 2-pin 0.1” Header (QTY 4)
  - Other
    - 0.1” 2-pin Jumper (QTY 4)
- Microscope / Magnifying Glass / Calipers (optional)

# Visual Inspection

A simple visual inspection of the DUT includes:

1. Board thickness Design ______ Measured: _____
2. Board dimensions Design ______ Measured: _____
3. Warpage: Verified _____
4. Short circuit, bridge, open circuit, voids Verified _____
5. Surface quality (scratches, scrapes, burrs, etc.) Verified _____
6. Holes and Vias hole drilled, plating present Verified _____
7. Add a serial number to the DUT with permanent marker. Boards should be numbered with this format: <Abbreviated Name>-<Number>-<Revision> for example the first board would be labeled ID-001-A for Breakout Board, 001-006 for the unique identifier and A for the revision.

# Fit Check

Not required for the Ideal Diode PCB

# Soldering

## SMD Soldering

1. Apply solder paste to all SMD pads
  a. Note, if a component won’t be populated for whatever reason, do not apply solder paste. Bake boards soon after placement.
2. Place all SMD resistors (R1, R2), capacitors (C1 – C13) and ICs (U1-U5)
  a. I find it helpful to have a printout of the schematic and mark off when a component is placed on the board. This prevents DNP (Do Not Place) components from getting populated.
3. Bake boards following instructions for the specific oven.

### Soldering Inspection 1

1. Verify there are no shorts between adjacent solder joints. Using a magnifying glass or microscope is useful. Adjacent pins on the controllers need to be inspected carefully
2. Verify all solder joints have the appropriate amount of solder.
3. Heat up any un-melted solder paste with an iron if necessary.
4. Touch up any solder joints with an iron if necessary. Use hot air if you are trained with that tool.

## Through Hole Soldering

1. Insert the screw terminals P1-P9 and solder one pin on each component. Ensure that the component is flush to the PCB. Reheat the solder joint and adjust the component if it is not flush. Then solder the other pins.
2. Insert the 0.1” headers in P10-P13 and solder. Ensure that the component is flush to the PCB. Reheat the solder joint and adjust the component if it is not flush. Then solder the other pins.

### Soldering Inspection 2

1. Repeat the same steps as soldering Inspection 1

# Testing

This board is relatively simple, so the electrical testing is relatively short. For other PCBs, the electrical testing section will be more in-depth.

## Electrical Testing

### Continuity / Short Circuit Testing

1. Using a digital multimeter set to continuity mode, verify there are no shorts between pins. It’s useful to be on “beep mode”.
  a. My strategy is to hold the red multimeter lead on pin one, then contact all other pins. Then move the red multimeter lead to pin 2, then contact all other pins.
  b. Verified _____

### Ideal Diode Operation

#### Single Input Voltage Range Testing

1. Populate P10-P13 with a 0.1” 2-pin jumper to enable Shutdown Mode on each controller
2. Connect a bench power supply to terminals P1 with the correct polarity. Set the current limit to 300mA. Set the supply to 10V, but do not enable the supply
3. Use a DMM to measure the output voltage. Verify output voltage on P5-P8
4. Enable the Bench Power Supply
5. Remove the Shutdown Jumper on P10.
6. Record the output voltage Voltage _____
7. Disable the Bench Power Supply and set it to 14V
8. Enable the Bench Power Supply and record the output voltage Voltage _____
9. Repeat Steps 1-8 for P1-P4

#### Multiple Input Voltage Range Testing

1. Connect the power supply to P1 and P2 set to 10V. Set the current limit to 300mA. Keep the supply disabled.
2. Populate the shutdown jumpers on P10-P13
3. Probe the output on P5-P8
4. Enable the bench power supply
5. Remove the shutdown jumper on P10 and P11
6. Record the output voltage Voltage _____
7. Carefully, probe the Gate Voltage on Pin 1 of U2 and U3 Voltage _____
  a. Ensure that both are operating
8. Disable the Bench Power Supply and set it to 14V
9. Enable the Bench Power Supply and record the output voltage Voltage _____
10. Repeat Steps 1-9 for P2 and P3, P3 and P4, P1 and P4, P2 and P4 (as time allows)

#### Multiple Supplies Voltage Range Testing

1. Connect the primary bench power supply to P1 and the secondary to P2. Set the current limit to 300mA.
2. Populate the shutdown jumpers
3. Set P1 to 11V, set P2 to 11V
4. Remove the shutdown jumper P10.
5. Record the output voltage Voltage _____
6. Remove the shutdown jumper P11
7. Record the output voltage Voltage _____

#### Battery Integration

1. Repeat the Ideal Diode Operational Tests with a real LiFePO4 batteries

### Current Sense Amplification Testing

1. Configure the Badgerloop mini-load bank to 6Ohms. (Adjust the series-parallel configuration, see Brandon Hahn for details) to draw ~2A. Connect to P5
2. Populate the shutdown jumpers
3. Use a secondary power supply to provide 5V to P9. Tie grounds of both power supplies together. Set the current limit of the secondary supply to 30mA.
4. Connect a bench power supply to P1. Set the current limit to 2.5A.
5. Remove the shutdown jumper and enable the power supply
6. Record the current output from the supply (Either the digital readout or use a clamp meter) Voltage _____ Current _____
7. Record the output voltage across pins 2 and 3 of P9 Voltage _____
8. Verify the amplified output voltage corresponds to changes in current by adjusting the power supply output voltage.

## Integration Testing

Integration testing involves testing the interfaces between the DUT and any other PCB, connector and mechanical enclosure the DUT will nominally interact with.

1. Verify the PCB mounts properly in the enclosure. Verified _____

## Thermal and Vacuum Testing

1. As time allows, perform thermal and vacuum testing. This test could be combined with current sense amplification testing. Use a thermal camera, focusing on the FETs and shunt resistors

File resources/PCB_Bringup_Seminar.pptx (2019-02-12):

## PCB Bring-up Seminar

2/14/2019 & 2/15/2019
Ryan Castle

## Objectives / Questions to Answer

- Developing Production Hardware
- Where do I find information to build a board?
- What Atlium tools do I need to know how to use?
- What materials do I need?
- Soldering 101
- Build up test PCBs

## End Goal

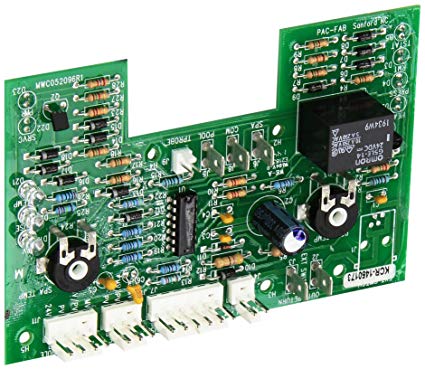
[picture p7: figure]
Image result for circuit board

- Functional Circuit Board capable of going into the pod
  - Populated PCBs
  - Soldering components is only ½ of the task
  - Bring-up instructions include basic testing information
- Be able to blame issues on the software and controls team

## Disclaimer

- We’ve spent a lot of time designing these PCBs and have spent ~$800 on components (~$2000 including sponsored components/PCBs)
- If you aren’t sure, ask
  - Definitely possible a mistake was made in schematic design or layout
- Practice on a test PCB
- Follow bring up instructions closely
- Inspect, inspect, inspect before you power on
  - No boards should be powered on for the first time without approval from Ethan or Ryan
  - Magic Smoke
- Mistakes are ok, we just want to avoid them
- Material might be really boring if you’ve done this before

## Altium Repository

- https://github.com/badgerloop-software/podiv-altium
- Primary source for all PCB information
- Possible to build a board from outputs
  - However, cloning the repo can speed up process
- Schematics, Layout files
  - Podiv-Altium/board_release/<pcb_name>/<revision_letter>/output/<*SCH*>
- Bringup Documentation
  - Podiv-Altium/bringup/<pcb_name>/<pcb_name>_bringup.docx

## Altium Tools

- Search for a Reference Designator (R1, U3, LED2)
  - In Schematics: <CTRL> + <F>
  - In Layout: <J>+<C>
- More information on a component
  - In Schematic:
    1. Double click on Component and the properties window will appear
    2. Click on the Properties Tab
    3. Manufacturer, P/N, Digikey P/N, link will appear.
    - Disclaimer: Sometimes, the parts to be populated won’t match with what’s in the schematic. This is because sometimes 2 components will have the same footprint or a BOM change was required for part availability

## Material Required

- See Bring-up Documentation
- Example for Ideal Diode PCB:
  - P4_LV_IdealDiode_001_REVA PCBs
  - Soldering iron
  - Solder
  - Solder Paste
  - Side cutters (snips)
  - PCB BOM
  - Oven

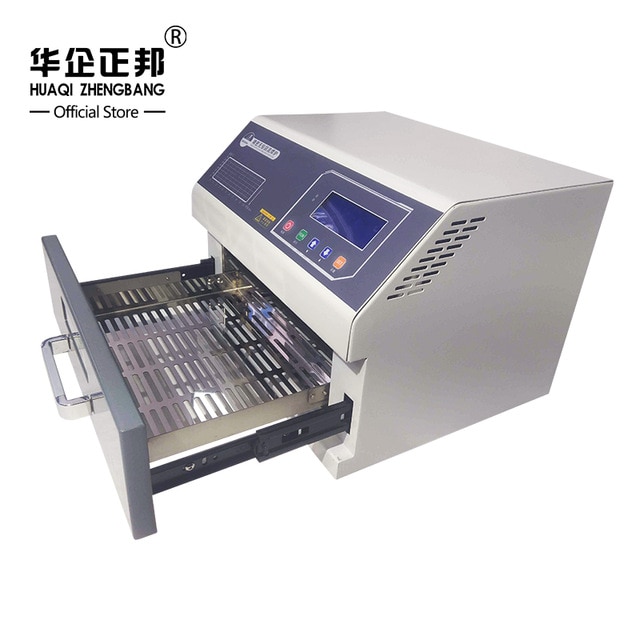
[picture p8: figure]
Image result for solder oven

## SMD Soldering

- https://mediaspace.wisc.edu/media/ECE370PowerSupplySM2-DVD/0_qaluf0im
  - Courtesy of Mark Allie, ECE 370
- Check Oven Settings
  - For this seminar, see if other groups are almost ready to use the oven. Possible to do multiple boards at once.

## What do I do if I find a problem with a board? Feature Request?

- Possible Answers:
A. Scream
B. Shout
C. Ignore it and hope it will go away
D. Submit a Feature Request or Bug Report on Github

Answer: All Except C
https://github.com/badgerloop-software/podiv-altium/issues

## Bring-up PCBs

- 2-3 people per PCB
- Boards:
  - Test PCBs (x2)
  - Processor (x5)
  - Ideal Diode (x2)
  - High Voltage Battery Breakout (x6) (Through Hole Only)
- Parts are all in the Digikey Box
  - Probably going to be a bottle neck. Be patient

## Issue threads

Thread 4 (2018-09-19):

Power Supplies -- 3.3V Rail

rcastle1, 2018-09-19:
Rough Requirements:
5A Supply
+- 5%
Input Voltage 10-15V
Utilizing the LTC8642S

vkottler, 2018-09-20:
5A on a 3.3V rail seems like a lot, we probably want to look at some of the block-level components we expect and see and maybe go with a less heavy-handed solution (unless you already have a good idea of where that requirement comes from)

rcastle1, 2018-09-30:
Switched to using the LT8650S for 5 and 3.3V rails. Schematic capture complete

Closed 2018-10-07.

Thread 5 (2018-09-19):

Power Supplies -- 5V Rail

rcastle1, 2018-09-19:
Rough Requirements:
* 8A Supply
* +- 5%
* Input Voltage 10-15V

Utilizing the LTC8642S (Might look into other supplies though)

vkottler, 2018-09-20:
Where does the choice in IC come from? Also [here's the datasheet](http://www.analog.com/media/en/technical-documentation/data-sheets/lt8642s.pdf) for any other readers out there

vkottler, 2018-09-20:
Duplicating some of the discussion between the two issues but wondering where 8A requirement comes from on the 5V rail? (not saying it's unreasonable just wondering if we've characterized it)

[BeagleBone ref manual](https://github.com/beagleboard/beaglebone-black/wiki/System-Reference-Manual#54_Power_Management)'s blurb about power management makes it sound like it should stay < 1A draw for example

rcastle1, 2018-09-21:
I'll add in the parametric search I did.  That gave me about 10 options to look through. Looked for meeting some arbitrary input/output requirements, part availability, plus a few nice to haves in a power supply (Pgood pin, integrated caps, silent switcher). Linear has great technical support too and I've used a similar component in previous designs.

Current requirements were pretty arbitrary, but purposely kept high as we're not sure what this will be powering in the future. Bringing down  to 4A didn't add many options. Over-powered is better than under-powered here I guess, but yeah getting power requirements from IO boards and processors should be done by @kevin asap.

Haven't looked into 3.3V supplies much. Although if I'm the only one doing any power design I'm going to be partial to not doubling my workload (Not a direct copy from one to another, but usually changing out FB resistors and compensation components and redoing the math)

vkottler, 2018-09-21:
I notice you wrote `No need for dual outputs` for the [ADP2325](https://www.digikey.com/product-detail/en/analog-devices-inc/ADP2325ACPZ-R7/ADP2325ACPZ-R7CT-ND/3071273), but isn't "dual outputs" what we're actually looking to implement overall?

Also, any reason most of these are QFN? Personally I would almost like to make "not QFN" a requirement just so we have a fighting chance at putting our own components down

rcastle1, 2018-09-30:
Switched to using the LT8650S for 5 and 3.3V rails. Schematic capture complete

Closed 2018-10-07.

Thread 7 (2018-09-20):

BeagleBone footprint + base mezzanine board geometry

vkottler, 2018-09-20:
Just a task stub, we'll need a footprint for the [BeagleBone](https://github.com/beagleboard/beaglebone-black/wiki/System-Reference-Manual#71_Expansion_Connectors) if we intend to use it and want to start thinking about the board geometries sooner rather than later

vkottler, 2018-09-24:
@rcastle1 what would be the best library to add something like this to? `connector`?

rcastle1, 2018-09-24:
I'd say connector if it's only going the 0.1" header rows.

rcastle1, 2018-10-03:
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

Couple of things about this configuration--

All external connectors on the same side and are board mount. Not sure if that's optimal, but I haven't seen a CAD model of the pod so I have no idea, but one side seems like a safe bet.

Beaglebone would be mounted with the bottom up for easy removal. center board would would not be removeable without removing side boards first. Given the sparse circuitry on this board, all components on the top side, I don't think we will have to take this board out often.

Side boards should have enough clearance to remove external connector, undo mount screws, and slide to the left or right out of the processor-side D-sub

Case would be made of sheet metal (www.protocase design?). Ideally we'd be able to see status LEDs so a clear cover and good positioning in the pod would be great.

badgerbricker, 2018-10-18:
@rcastle1 @ezraboley are you guys working on this?

Closed 2019-02-08.

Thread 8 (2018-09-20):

Backplane board gemoetry and layout

vkottler, 2018-09-20:
Just a task stub, should be re-assigned and updated w/ any commitments / decisions we make on this front

rcastle1, 2018-09-23:
For future reference we have narrowed in on these two concepts. The primary difference between them is the number of boards.

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

The 2-board concept has a generalized processor and power board which plugs into module-specific IO board. This option simplifies our pinouts, reduces the number of connectors and therefore reduces board/BOM cost.

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

The 3-board concept has a generalized power board, a separate processor board, and a module specific IO board. There is some added work of selecting another board-to-board connector and ensuring the two designs pinouts match, however this has the added advantage of being able to work in parallel not only for schematic capture and layout, but initial bring up of the power supplies and processor boards. For example, the processor board could have a bench power supply connected while the power supply card is being brought online.

The key determining factor between the two options will be the number of people that are willing to commit to own a board, as collaboration on the same board across time zones may be difficult in Altium and Git.

For either option, the enclosures will fit in an enclosure designed by the fabrication team (actual MEs). The electrical responsible engineer (RE) will work the the mechanical RE to ensure sufficient space is allocated, connector choice is suitable for assembly and disassembly, and internal harnesses are eliminated.

vkottler, 2018-09-26:
`This option simplifies our pinouts, reduces the number of connectors and therefore reduces board/BOM cost` can you show some evidence for that please @rcastle1

vkottler, 2018-09-26:
`There is some added work of selecting another board-to-board connector and ensuring the two designs pinouts match`?? "board-to-board" connector is 0.1" headers where the processor and IO boards use the same pinout, so that work is actually already done..

vkottler, 2018-09-26:
I don't think we want pneumatic-facing components on the "navigation IO" board, we want just sensing.

keving98g, 2018-09-26:
I was under the assumption that we were going to separate our braking hardware from our navigation inputs. As in put them on separate boards.

vkottler, 2018-09-26:
Yeah, that's what I am proposing

rcastle1, 2018-09-26:
The pinouts will be exactly the same? That seems like a premature assumption. Either way it’s not too much more work, but increasing connector count is non trivial. I’m still going to prefer D-sub for board-to-board connections due to the advantages I’ve listed previously, but at this point whatever.

That’s fine with pneumatic facing components. I have no idea what the physical layout of the pod will be and haven’t seen an overall block diagram of the pod which would be very helpful for the task of defining how many modules and what are their functions.

On Sep 26, 2018, at 7:12 AM, Vaughn Kottler <notifications@github.com<mailto:notifications@github.com>> wrote:

Yeah, that's what I am proposing

—
You are receiving this because you were mentioned.
Reply to this email directly, view it on GitHub<https://github.com/badgerloop-software/podiv-altium/issues/8#issuecomment-424730798>, or mute the thread<https://github.com/notifications/unsubscribe-auth/AYo7R2WFqQlZ_dvjMZ9wpMKQp-yZ05j9ks5ue4togaJpZM4WxeZM>.

vkottler, 2018-09-26:
You don't need to make "assumptions" for things you have full control authority over, if you want the pinouts the same you can make them the same and use the same schematic component, or you can make them different and have orphaned pins or do whatever you want.

@rcastle1 if you want a BeagleBone processor+power board variation and a microcontroller processor+power board variation is that the intended approach? N possible implementations of each board?

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

Why is something like Ethernet being routed through something other than an RJ45? I also don't think we'd want JTAG coming out of this style of connector (just want 0.1" shrouded headers that natively connect to the programmer).

vkottler, 2018-09-26:
`I’m still going to prefer D-sub for board-to-board connections due to the advantages I’ve listed previously, but at this point whatever` we're not in disagreement that for two-boards in the same XY plane D-sub (right-angle) is a good choice. One of the architectures has that configuration (two-board) the other doesn't ("mezzanine" style, boards parallel but with a +z coordinate). If the friction of the two, 2xN shrouded headers isn't enough you can add mounting hardware to secure it (same solution used by D-sub).

rcastle1, 2018-10-10:
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

rcastle1, 2018-10-10:
This is the really rough layout I'm thinking for the beaglebone breakout board. For reference, this board needs to be the power passthrough to the IO board, a breakout board for the beaglebone to the IO board, and have  have CAN headers. I added in a pressure sensor circuit and will also add in IO circuitry we know we want on both HV and LV boards.

Depending on the additional circuitry, we can condense a bit on the right side. Couple things I know are not correct -- Beaglebone is floating, need to add 0.1" female headers, that IO connector is an 80 pin Misc devices part, need to replace with an appropriately sized loop-library component.

vkottler, 2018-10-10:
How many indicator LEDs?

rcastle1, 2018-10-10:
Has none at the moment. Add a 8 pin GPIO expander for that?

vkottler, 2018-10-10:
That would work, with 8 pins I think 4 for LEDs and 4 for toggle switches for configuration options would be nice

Closed 2019-02-08.

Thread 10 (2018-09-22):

Board Outline and Enclosure Design

rcastle1, 2018-09-22:
- [ ]  Finalize connector style for board-to-board connector.
- [ ] Spec harnesses connector style for external IO and power distribution. We want to avoid internal harnessing here.
- [ ] Reach out to protocase.com or others for sponsorship.
- [ ] Spec a layout size estimate for processor and IO boards. Get an initial size for the enclosure
- [ ] Create a .dxf file for the board outline
- [ ] Integrate enclsure to the full pod assembly (how do we mount to the pod. Is it removable? Vibration testing)
- [ ] Spec and order all fasteners required
- [ ] Get PCB .step file after components have been placed and verify alignment, clearance with enclosure. Pay particular attention to clearances for inserting and removing boards.
- [ ] Order or fabricate enclosure.
- [ ] Assemble enclosure
- [ ] Deploy system

vkottler, 2018-09-22:
Should we build a list of candidate connectors on here or somewhere else?

rcastle1, 2018-09-22:
Here's fine.  Here are the one's I've been looking at. (Just linking individuals, would need mates)
DSubs
* https://www.digikey.com/product-detail/en/te-connectivity-amp-connectors/6-5173277-2/A114311-ND/2203212
* https://www.digikey.com/product-detail/en/te-connectivity-amp-connectors/5787170-4/A31806-ND/807155
* https://www.digikey.com/product-detail/en/amphenol-fci/ICD26S13E4GX00LF/609-2804-ND/1090328 (May have to go 2 of these)
* https://www.digikey.com/product-detail/en/te-connectivity-amp-connectors/5747842-6/A32102-ND/808657
* 0.1" Headers
* ~~ET60T/S~

This issue could also be split into sub- issues if necessary too.

rcastle1, 2018-09-23:
I'm still thinking we should only have two boards (processor and power on one, module specific IO on the other) that have two right angle male and female connectors on the same xy-axis. It seems like additional complexity to increase our board count. Can you elaborate on the advantages of doing a U-shaped geometry and three boards?

rcastle1, 2018-09-23:
For external harnesses we should not use D-subs or 0.1" headers. Soldering a cable harness to that type of bulkhead is very error prone and easy to short, pull out. Crimps are a lot more solid.

vkottler, 2018-09-23:
With "two right angle male and female connectors on the same xy-axis" the enclosure would be the rigid body that both boards attach two and ensure a solid connection, the procedure for getting the board(s) into the enclosure would be connecting them then fastening them both in. If a board needed to be taken out it would need to be unfastened then disconnected (nothing wrong with that, just something to consider).

The value proposition of a monolithic power+processing+etc board with N IO boards works fine. Consider that it's not possible to parallelize work on that monolithic board, one person has to own it.

I'm not proposing a U-shaped geometry anymore (see `"am having second thoughts on cards that plug into the backplane being perpendicular to it"` above). I'm proposing one base board that creates power rails and has the 0.1" shrouded header that provide power and generic connections to one or more other sets of the same header configuration.

vkottler, 2018-09-23:
I prefer not having a monolitic "power *and* processing *and* . . ." really just so that the work can be parallelized. I don't see where complexity is added by making one thing into multiple boards if we're already scoping a "common interface" with this architecture

vkottler, 2018-09-23:
I prefer not having a monolitic "power *and* processing *and* . . ." really just so that the work can be parallelized. I don't see where complexity is added by making one thing into multiple boards if we're already scoping a "common interface" with this architecture

rcastle1, 2018-09-23:
I think if we have boards on standoffs, it would be possible to unscrew one board, slide it out of the connector, and pull it out. Plus if we keep all components top side and don't have a bunch of internal harnesses, basic rework should be possible in the enclosure.  `Pay particular attention to clearances for inserting and removing boards.`

I've worked on boards with multiple schematic designers. Layout is the harder part to collaborate on definitely. (In Cadence, you can have real time work on a layout pretty neat to watch)

keving98g, 2018-09-26:
Matt and I had met yesterday along with Matt and we had shared our initial thoughts about enclosures and set up our design goals for going with custom enclosures (along with looking nice).

- Follow the change of decreasing/omitting internal harnessing with open/inverted enclosure design for easier testing and debugging
- Enable further customization (or partially customization) if needed between different modules.
- Decrease weight and design with full integration (putting on the pod) in mind.

Matt is working on a simple model with the ideas that we had come up with and that will be posted here.

rcastle1, 2018-09-30:
Any progress on board outline / mount hardware / connector orientation @keving98g @ matt?

Closed 2019-02-08.

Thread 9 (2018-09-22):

Power Supply DVT Requirements Spec

rcastle1, 2018-09-22:
Spec what requirements need to be performed on a power supply circuit. See this [readme](https://github.com/badgerloop-software/podiv-altium/blob/processor_power/src/power/README.md) for more details on the types of tests available.

rcastle1, 2018-09-22:
Copying over slack conversation
Ryan Castle [Sep 19th at 10:27 PM]
Anyone know of any vector network analyzers (VNAs) available on campus?

73 replies
Ryan Castle [1 day ago]
http://ridleyengineering.com/hardware/ap310-analyzer/intro-ap-analyzer.html would prefer this but it’s $15K

Vaughn Kottler [5 hours ago]
what's this particular inquiry about

Ryan Castle [5 hours ago]
Looking into measuring  power supply loop gain and pjase (edited)

Vaughn Kottler [5 hours ago]
is that not something you trust from the datasheet?

Ryan Castle [5 hours ago]
It’s not a data sheet characteristic

Vaughn Kottler [5 hours ago]
and what is the notion of "phase"? When is t0

Vaughn Kottler [5 hours ago]
lay the value proposition on me of measuring that

Ryan Castle [5 hours ago]
Highly dependent on choice of external components (input /output caps + compensation)

Vaughn Kottler [5 hours ago]
do you look for resonance w/ this type of measurment? Is this for choosing a switching freq.?

Ryan Castle [5 hours ago]
I will post a summary of what the test is and it’s benefits when I get back from work. Git issue?

Ryan Castle [5 hours ago]
The theory behind is is non-trivial but the test itself is pretty basic

Vaughn Kottler [5 hours ago]
yeah make an issue that captures the problem statement of needing to make some of these measurements

Ryan Castle [5 hours ago]
There are other ways to test power supplies, initial inquiry was to see what we have access to.

Vaughn Kottler [5 hours ago]
right, so we need a contingency plan if we don't have access to equipment we'd need to complete verification of a design etc.

Ryan Castle [5 hours ago]
http://www.ti.com/lit/an/snva364a/snva364a.pdf here’s a link to the type of test in the meantime. It can also be done with a scope and signal generator if necessary

Ryan Castle [1 hour ago]
https://github.com/badgerloop-software/podiv-altium/blob/processor_power/src/power/README.md I got through some of the different tests we can run for power supply DVT.

Ryan Castle [1 hour ago]
all I got for tonight. will be on tomorrow.

Vaughn Kottler [1 hour ago]
I still don't understand the risk associated with skipping some of this DVT and substituting our actual application loads as verification

Ryan Castle [1 hour ago]
at this point im putting out what the industry standard way of doing things is.

Vaughn Kottler [1 hour ago]
I see the merit for the case where a power supply is being designed to spec for distribution but in this case I don't fully understand what guarantees we want, what we'd actually be looking for and what types of things require configuration changes or a complete re-spin of a board

Ryan Castle [1 hour ago]
power supply design is really tricky and we should do it right, in my opinion. there are a lot of corner cases that we could really experience (hot day in LA, Battery voltage is funky, variably loads) we don't want to get burned.

Ryan Castle [1 hour ago]
a lot of the time it's as simple as changing a capacitor out

Ryan Castle [1 hour ago]
if we're trying to say this is a general purpose board then we really don't know what the application will be like

Ryan Castle [1 hour ago]
and we have no sense of the margins

Ryan Castle [1 hour ago]
I'm sure that I'll end up doing this when I get back and don't really expect anyone else to figure out how to do this kind of thing. I spent 8 months on co-op learning how to do this

Ryan Castle [1 hour ago]
We need to test transients, we need to measure frequency response (edited)

Vaughn Kottler [1 hour ago]
Can you go into more depth in terms of failure modes from specific load scenarios to make that statement true for those of us who don't know why we would need to do that

Vaughn Kottler [1 hour ago]
How does `30 degrees of PM and -5dB of GM` manifest as a failure

Ryan Castle [1 hour ago]
So if you have insufficient margins under controlled lab conditions (i.e. not LA summer weather, not after running our supplies for hours on end, etc.) if you lose more margin due to a number of problems that can come up, and phase and gain are both near zero at the same time, the supply will go unstable.

Vaughn Kottler [1 hour ago]
unstable meaning resonance on the output? What does unstable mean

Ryan Castle [1 hour ago]
unstable could be a number of things. It could mean the supply forces itself into shutdown, it could ring (like a high amplitude sinusoid on the output). One supply I worked on had about 15 deg of PM and at like 10 deg above room temp it would go between 2-3x higher than what vout was supposed to be and then zero.

Vaughn Kottler [1 hour ago]
From what input?

Ryan Castle [1 hour ago]
this one was like a 2.5V supply from 4.75 to 13.2Vin

Vaughn Kottler [1 hour ago]
So there was some kind of ramp-up profile on the input or the input was steady state?

Ryan Castle [1 hour ago]
input was constant from a rigol.

Ryan Castle [1 hour ago]
steady state load too

Vaughn Kottler [1 hour ago]
So at some nominal input voltage, a 10 degree increase in temperature led to failure of the supply? Input voltage, output voltage + current all in nominal operating ranges? What caused the failure there

Vaughn Kottler [1 hour ago]
What are the realistic "gotchas", I don't understand what kind of abstraction an off-the-shelf power management IC gets you if you have to do all of this

Ryan Castle [1 hour ago]
So that was an interesting solution to find. ended up changing a compensation capacitor to a higher value cap. We were using an X5S capacitor

Vaughn Kottler [1 hour ago]
Interesting, so that's an actual implementation mistake. Makes more sense

Ryan Castle [1 hour ago]
this test takes like 10 minutes to perform

Vaughn Kottler [1 hour ago]
Yeah I just don't understand if it's a one-step verification or like an iterative thing you have to do to design a power supply

Vaughn Kottler [44 minutes ago]
i.e. having this data allows you to characterize the capability of your supply?

Ryan Castle [43 minutes ago]
So all of the blue is user input. A lot of times data from manufacturers can be inaccurate or hard to lock into a single number
Capture.PNG

Vaughn Kottler [42 minutes ago]
What software is that

Ryan Castle [42 minutes ago]
You design the supply in software like LTPowerCAD, which gives you FRA simulations

Ryan Castle [42 minutes ago]
Capture2.PNG

Ryan Castle [42 minutes ago]
but you need to compare the simulation to real world test results

Ryan Castle [41 minutes ago]
(Another reason I wanted to use Linear Tech parts over ADI is PowerCAD is a really nice tool)

Vaughn Kottler [40 minutes ago]
Is it free?

Ryan Castle [40 minutes ago]
also btw those are just default solution values

Ryan Castle [40 minutes ago]
yeah it's free

Ryan Castle [39 minutes ago]
https://github.com/badgerloop-software/podiv-altium/blob/processor_power/src/power/README.md#getting-started Step 3

Ryan Castle [39 minutes ago]
really nice, can export to LTSpice as well

Vaughn Kottler [37 minutes ago]
So LT makes a power management IC, why would / should every user go through this process? Everyone has that unique of load scenarios? Just wondering how this isn't a solved problem

Ryan Castle [37 minutes ago]
So the design process is do a bunch of math following the datasheet to pick values for components, spec components, enter those values into powercad, adjust to optimize frequency and transient, then build the circuit and compare. If actual is close to predicted, you're good. if it's not, debug and change out components

Ryan Castle [33 minutes ago]
so they have a few sample solutions (which I'm guessing most users just copy and paste into their designs), but there are a lot of requirements you might have for a supply. For example, they usually use big components, way oversize inductors, you might need a certain output voltage tolerance, noise reduction, EMI filtering (which is magic to me, no idea), input / output voltage ranges, bulk capacitance, capacitor shortages, switching frequency... (edited)

Ryan Castle [32 minutes ago]
it's like any other engineering problem-- lots of variables to optimize

Ryan Castle [32 minutes ago]
sometimes sample solutions work, sometimes they don't

Ryan Castle [32 minutes ago]
usually where I start off from and then customize

Vaughn Kottler [28 minutes ago]
Yeah that makes sense, we have experienced plenty of headaches related to surface-level understanding of power management

Making a robust supply is a good way to create a layer of abstraction that allows you to just trust your rails on the other side and not design in hot fixes for supply corner-cases and deficiencies

Vaughn Kottler [27 minutes ago]
And, I don't have the same context as you but it doesn't sound like this is necessarily "highly iterative" or an insane time investment, but I still don't have a good grasp of "how close you can get" to what you want on your first try

Vaughn Kottler [26 minutes ago]
i.e how many power supply board revs would we need to plan for to be safe

Ryan Castle [25 minutes ago]
so in my experience, I've never had to change netlist (i.e. change layout connections). Usually it's changing component for component in the BOM

Vaughn Kottler [24 minutes ago]
Makes sense, footprint change(s) common?

Ryan Castle [24 minutes ago]
Yeah, usually 0805 -> 0805

Ryan Castle [23 minutes ago]
I'm about 50% on the 10 supplies I've designed for getting the sims to match reality on the first try

Vaughn Kottler [22 minutes ago]
Dang, well maybe we will have a chance here then

Ryan Castle [22 minutes ago]
Yeah, if you know what you're doing or are good at debugging, it's difficult but it's not magic

Ryan Castle [20 minutes ago]
our failsafe could be to design in pads for the off the shelf supplies too

Vaughn Kottler [20 minutes ago]
Yeah well now I'm questioning what sort of guarantees off the shelf supplies even provide

Ryan Castle [19 minutes ago]
My big concern with doing our own supplies is that we'll need it before I'm back

Vaughn Kottler [19 minutes ago]
Lab bench power supply / USB etc. is fine for dev

Closed 2019-02-08.

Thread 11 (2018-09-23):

Decide on Beaglebone

rcastle1, 2018-09-23:
Issue for discussion on the beaglebone vs. other processing options.

rcastle1, 2018-09-23:
i don't really have a stake in the the outcome of this discussion, but it's been going on for over a month and needs to be decided.

rcastle1, 2018-09-30:
What model beaglebone are you using @ezraboley ?

ezraboley, 2018-10-01:
[BeagleBone Black Rev C w/o wireless](https://github.com/beagleboard/beaglebone-black/wiki/System-Reference-Manual)

Closed 2018-10-15.

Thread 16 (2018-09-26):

Library TODO

rcastle1, 2018-09-26:
Make a component symbol for the following:
- [x] [40-Position Right Angle D-sub](https://www.digikey.com/product-detail/en/te-connectivity-amp-connectors/6-5173277-2/A114311-ND/2203212`)
- [x] [Shrouded 0.1" Header](https://www.digikey.com/product-detail/en/on-shore-technology-inc/302-S201/ED10524-ND/2794235)
- [x] [Right angle DB-9 RCPT](https://www.digikey.com/product-detail/en/assmann-wsw-components/A-DF-09-A-KG-T2S/AE10921-ND/1241800)
- [x] [Right angle DB-9 PLUG](https://www.digikey.com/product-detail/en/assmann-wsw-components/A-DS-09-A-KG-T2S/AE10968-ND/1241804)
- [x] 0.1" Headers, 1x2, 2x2, 2x3...2x10

Make a component footprint for the following
- [x] 40-Position Right Angle D-sub
- [x] Shrouded 0.1" Header
- [x] Right Angle DB-9 RCPT
- [x] Right Angle DB-9 PLUG
- [x] 0.1" Headers, 1x2, 2x2, 2x3...2x10

nickbeckwith, 2018-09-26:
Have the 40 position right angle d-sub almost ready. Might need help getting a 3d model and footprint for it though.

vkottler, 2018-09-26:
What's that 40-Position D-sub going to be for @rcastle1

vkottler, 2018-09-26:
@nickbeckwith @rcastle1 if there's no 3D model available through ultra-librarian or linked from the part on Digi-Key we might want to choose a different part

nickbeckwith, 2018-09-27:
@vkottler @rcastle1 Okay, I can't find any models through either so I'll look around for another part if it's still necessary

badgerbricker, 2018-10-04:
working on Right angle DB-9 RCPT making footprint

Closed 2019-02-08.

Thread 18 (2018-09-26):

Cap Library Schematics

rcastle1, 2018-09-26:
Please make schematic symbols for the following components. Some footprints should already be done.
- [ ] C4532X7R1E226M250KC (1812) -- needs footprint
- [ ] C2012X7R1E475K125AB (0805)
- [ ] CGJ2B3X7R1E104K050BB (0402)
- [ ] TNPW040231K2BEED (0402)
- [ ] C0402C100K3GACAUTO (0402)
- [ ] T520D337M006ATE045 (Tant 2924) -- needs footprint
- [ ] IHLP2020CZERR47M01 (Inductor 2020) -- needs footprint

rcastle1, 2018-09-26:
Note that we have some big capacitor libraries already, which are usually fine to use, but in some power design cases characteristics like ESR and ESL are important enough, or quantities are not available currently for those parts, so new parts are required

rcastle1, 2018-10-03:
No longer needed

Closed 2018-10-03.

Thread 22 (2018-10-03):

Power Board Review

rcastle1, 2018-10-03:
Review:
- [ ] Design information
- [ ] Schematics
     - [ ] Pinouts
     - [ ] Circuit Analysis
- [ ] Layout
     - [ ] Footprints
     - [ ] Power and GND planes
- [ ] BOM

Open TODOs remaining:
- [ ] Power Plane division
- [ ] Add links to D-Sub BOM
- [ ] Verify board outline is Ok with full assembly

rcastle1, 2018-10-15:
See Templates > SchematicPCBReviewChecklist for the review document. Let's close out this board by the end of the week. Tristan, you can do the primary reviewer, Austin, can you look over the checklist? Going through that list there are definitely things that need to be fixed on the power project before release.

rcastle1, 2018-10-15:
Normally the designer would make all edits from feedback, but I'm pretty busy with work and moving to a new AirBnB so if you wanted to make small changes after going through the checklist that'd probably be ok.

Closed 2019-02-08.

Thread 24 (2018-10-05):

Change out LEDs

rcastle1, 2018-10-05:
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

Should be a fairly quick project but it will walk you through all of the steps of making changes to a schematic in our workflow.

In the past we've had to pull out the oscilloscope to tell if CAN messages are sending. LED indicators will let us visually know that messages are sending/receiving. Unfortunately, I only have Red and Green LEDs, which usually indicate something right or wrong is happening, but in this scenario, sending/receiving may or may not always follow that binary, so I want to switch these LEDs to a neutral colors (orange and blue, although if you really want to pick a different color that's fine)

1. Spec out Orange and blue SMD LEDs (0603 preferabbly, check for a some that are in the same package as the existing green/red LEDs)
2. Add these parts to the library branch (including component links, 3D Models (color them too please!))
3. Make a pull request, get it approved
4. Rebase the beaglebone_project
5. Update the schematic with the appropriately colored LEDs
6. Commit, push changes. Don't make a Pull request here are this project is still ongoing, but push to remote so I can get the changes.

vkottler, 2018-10-05:
I think we want these normally DNP also

btobin86, 2018-10-24:
Submitted a pull request for the orange and blue LED components that were added to the schematic and footprint libraries

rcastle1, 2018-11-07:
what branch did you do this on?

btobin86, 2018-11-07:
Originally on libraries, but then you told me to move put it on
beaglebone_2 instead.

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

rcastle1, 2019-02-08:
complete. thanks

Closed 2019-02-08.

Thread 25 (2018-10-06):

TEMPLATES: Sample circuit

rcastle1, 2018-10-06:
Purpose of this circuit:
This circuit is designed to show new users how to follow the workflow for creating circuit snippets. It will not be used on the pod.

Requirements:
1. This circuit should take less than 1 minute to draw out for video purposes
2. This should use existing library components for ease of video making.

Responsible Engineer:

rcastle1, 2018-10-06:
Getting started on this circuit.

rcastle1, 2018-10-06:
created video and sample snippet. making a PR now

rcastle1, 2018-10-07:
Waiting on review/merge from @tsteiner4 then close issue.

btobin86, 2018-10-17:
Getting started on circuit. However, unable to add myself as an Assignee

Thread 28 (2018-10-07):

TEMPLATE: Retroreflective Sensor

rcastle1, 2018-10-07:
### Note:
See the Hyperloop Test Track Specification document in box (Badgerloop eyes only) located [here](https://uwmadison.box.com/s/ezaj20bkuyem90ak4xtz95dnn90fkpr2) for more information on navigation.

### Purpose:
The [QMIC](https://www.automationdirect.com/adc/Shopping/Catalog/Sensors_-z-_Encoders/Photoelectric_Sensors/DC_Rectangular/Retroreflective_(QM-z-CX-z-FE_Series)/QMIC-0N-0A) ([Datasheet](https://cdn.automationdirect.com/static/specs/peminirectqm.pdf) retroreflective sensor detects tape strips throughout the tube and triggers an interrupt input to the beaglebone. We calculate our position, velocity and acceleration from the retroreflective tape strip count. Once this is up and running, we will add in interpolation from the IMU for higher resolution.

### Circuit Description:
The QMIC photoelectric sensor is an NPN output type powered from 9-36V. The sensor could be powered from either LV Battery or 24V. It may be advantageous to use 24V as a constant source. When the circuit is active (i.e. tape is detected) the current will flow through the current limiting resistor and activate the optocoupler. This effectively converts the higher voltage signal into a low voltage signal that is able to be read in by the beaglebone.

You will need to also investigate the interrupt capability of the beaglebone. We have all of the circuitry for this circuit on hand an in through hole form, so you should also build the circuit and test it out. It would be great to work with @ezraboley or @ethanlink17 to write some code to verify the compatibility with the beaglebone.

### Pod III Schematic:
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

Full [Navigation Schematic](https://uwmadison.box.com/s/fuog5mmjrutf7e8z87q4elr5liqnag0e)

keegangruss88, 2018-11-01:
I made this for the new project list. I need to spec out the parts and make the footprint yet.

Closed 2019-02-08.

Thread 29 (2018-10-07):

TEMPLATE: Accelerometer

rcastle1, 2018-10-07:
### Purpose:
Acceleration measurement and velocity interpolation.

### Circuit Description
This one's not too bad circuit wise. This basically requires a breakout to the [MTI-3](https://www.digikey.com/product-detail/en/xsens-technologies-bv/MTI-3-DK/MTI-3-DK-ND/5325385) Sensor. Actual mounting of the sensor is a little more tricky. We'd like the sensor to be mounted directly on the PCB as opposed to a short harness. Although, having the ability to adjust the sensor so it can line up with the direction of travel in the pod would be good. It's up to the RE.

### Pod III Schematic
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
Full Navigation [Schematic](https://uwmadison.box.com/s/fuog5mmjrutf7e8z87q4elr5liqnag0e)

vkottler, 2018-10-26:
I think deciding what interface to expose for use with the proposed module architecture is going to be hard to do right now, this issue can just encapsulating upstreaming a high-quality schematic symbol and footprint.

btobin86, 2018-11-04:
Pushed the schematic symbol and breakout board schematic

Closed 2019-02-08.

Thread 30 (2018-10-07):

TEMPLATE: Wheel Speed Measurement

rcastle1, 2018-10-07:
### Purpose:
We want to have measurement of wheel RPM. This is a pretty open ended design project, as there's not a particular way we've done this in the past. Eventually, we want to compare wheel RPM velocity measurements and compare that to the retro tape method to see how much we are slipping.

### Circuit description:
Up to you. We could do the same retro circuit on the wheel and you can look at issue 26 for that, or you could design a fresh circuit. You should probably talk with Nathan Berg (propulsion) or James Ewald (stability) to see how this should be integrated into the pod.

Closed 2019-02-08.

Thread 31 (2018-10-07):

TEMPLATE: Front / Distance Sensor

rcastle1, 2018-10-07:
### Purpose:
We have to end the run within 100 ft of the end of the tube. This circuit will primarily be speccing out an affordable distance sensor that can accurately determine position within 100 ft. This is a little challenging as  we're in such an enclosed environment. The one we looked at last year was like $2000, but for this we probably have 100-200 for this sensor.

### Circuit description
Most sensors will have a 4mA-20mA output, scaled to the total distance range of the sensor. So for this circuit you place a resistor in series with the output and measure the voltage across the resistor and scale the voltage to a current using V = I * R

badgerbricker, 2018-11-07:
# In Price Range:
## LIDAR-Lite v3HP and  V3
* v3 $129.99 40m 5V DC
     * https://www.sparkfun.com/products/14032
* v3HP $149.99 40m 5V DC faster sampling rate
     * https://www.sparkfun.com/products/14599
## RS232 50M and 100M Versions
* $47.41-$53.51 (its on alibaba though)
* Input: 23.0V-3.2V
* accuracy +/- 1m
* three wire serial interface
     * 100M: https://www.aliexpress.com/item/100M-Laser-ranging-module-digital-sensors-Distance-Measuring-serial-port-USB-to-RS232-TTL-signal/32702749857.html
     * 50M: https://www.aliexpress.com/item/50M-small-size-Laser-ranging-module-digital-sensors-Distance-Measuring-serial-port-USB-to-RS232-TTL/32761973599.html
     * on amazon: still not a lot of detail https://www.amazon.com/Distance-Serial-Sensor-Finder-Module/dp/B07G4F14RR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

# Out of Price Range
## Parallax Lser Rangefinder 120M
* 120M I2C 5V DC
* $313.88
* Voltage Range 0-3.30V
     * https://www.digikey.com/product-detail/en/parallax-inc/28054/28054-ND/6009003
## Range Finder 1000M
* $375
* +- 0.5m(400m)
* 3V 120mA
     * https://www.amazon.com/Distance-Serial-Module-Rangefinder-Measurement/dp/B0761ZLYSN

badgerbricker, 2018-11-07:
# Information Needed
1. breaking distance of pod
     * need to know how much distance warning needed will it be able to stop within 100 feet or does the sensor need to have a longer range to trigger stopping earlier
2. speed of pod before breaking
     * check max sampling rate
3. what interfaces are avaible on the microcontrolers? Which one will it interface with?
     * I2C manditor? Analoge OK?
## Next steps
1. Pick sensor
2. Create part in Altium
     * Schematic and Footprint
3. Create circuit in Altium
4. Add as snipet

rcastle1, 2018-11-07:
For this sensor to be worthwhile, we should think about how it will be used in the control loop. My comments should be generic to whatever sensor is selected, but a specific one may alleviate some concerns or cause new ones.

They will have a beta angle that determines how large the field of vision will be. The sensor will detect the side walls for most of the run, until we are a range of the end of the tube that the geometry works out. An excel tool with some of the math worked out could be useful.

There are a few options for the control loop I can think of for using the sensor:
1. Ignore data from this sensor until we can detect that it's actually hitting the end of the tube. (how this is done is probably sensor dependent, I'm not sure if this is actually possible)
2. Rely on the redundancy in retro tape to give us an exact position with 100-ft resolution. Detect when we are at the last tape strip 100ft away from the end of the tube (or if we know the sensor has greater usable range, some retro set point) and then start reading the data.
3. See if we can determine that in the tube, we will be reading a constant value until we near the end of the tube, where the behavior changes, and go from there.
4. Talk to an applications engineer from one of these sensor companies.  You might have to be persistent to get a hold of someone.

Reasons for not including the sensor:
1. If we are already ignoring data and relying on retro tape for 100 ft resolution and the requirement is to stop within 100ft of the end, why do we need this extra sensor?
2. If the run profile is still to start, go to a high speed, stop, then go for a low speed, do we just rely on manual control (with appropriate signal-loss fail safes)?
3. Testing the sensor would only really be possible at scale when we get to California and they let us in the tube. We've never made it before, and I'm assuming that we will have other problems to work out that week, so unless we can prove the sensor operates as we understand it on the bench and can prove that this will scale, this should be descoped. I'm all for buying one for $100 or whatever and trying it out as our advisers clearly wanted us to have one last year.

@badgerbricker You should talk with @ezraboley and @vkottler about any sensors with a digital interface. I would also be a avoid solutions that come from websites like aliexpress.

rdaruwala, 2018-11-07:
To pitch in for the interfaces -- We should be able to deal with most. I2C/SPI/UART/Analog are all fine.

Regarding the control loop:

From my (limited) experience with range sensors, they tend to return an "no range found" data value when they don't have data. Though I imagine the system will vary depending on the sensor. I'd suggest reading it throughout the run, should be a good redundancy to have.

Braking distance is a really important factor we need to consider. Do we have an approximate number?

badgerbricker, 2018-11-08:
The LIDAR-Lite V3 by spark fun is only $129 as mentioned above has a 4x2m radian divergence (elliptical) I would assume that is at the max measure distance of 40m but sparkfun doesnt specify. I2C compatable so it should be able to talk to the beagle bone just fine. Also its made by sparkfun so its will be good quality. I think this sensor is looking promissing but we need to know:
* Would 4x2m divergence avoid hitting the walls of the pod? /What is the radius of the pod?
* Would 40m be enough for braking distance if we choose to rely on this sensor for position? Alternatively we could use it to validate the slow crawl to the end of the tunnel in addition to the retrorelfective strips.

I understand that it might not be necessary to have this sensor since we have to retros but it might be a nice secondary system to validate the retros Im not sure how accurate the retros have been in the past.

Closed 2019-02-08.

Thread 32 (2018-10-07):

TEMPLATE: Solenoid Driver and Feedback

rcastle1, 2018-10-07:
### Purpose:
Solenoids are the main way we interface with the pneumatic system (along with pressure sensors). Solenoids are basically just inductors electrically, and mechanically they allow air to flow or not to flow. To activate a solenoid, you have to apply a voltage aross the coil.

What we want to add in this year is current feedback. We know that we are driving a FET, but we aren't sure that current is actually flowing through the solenoid. This isn't quite perfect as there's a possibility that the solenoid is mechanically stuck open or closed so ideally we'd have limit switch feedback, but that type of solenoid is much more expensive. So this is a compromise. If you'd like to work with the braking team to find solenoids with switches that aren't ridiculously expensive, then we can switch this circuit feedback to the limit switches.

It may also be a good idea to figure out a way to have an LED directly on the solenoid to tell what solenoid is actuated and what solenoid is not. Ask an electrical guy from Pod III about why.

### Circuit Description:
This is a basic FET driver circuit. A digital output from the I2C IO Expander drives the gate of an NMOS FET. The solenoid is connected to 24V and the Source of the FET. Drain is connected directly to GND.
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

For feedback, using the [INA240](http://www.ti.com/product/INA240) would be a good idea as a current measurement. There's even a sample circuit for this exact thing.

rcastle1, 2018-11-04:
these are all components in the misc. devices or misc. connectors library.

rcastle1, 2018-11-04:
are we going to add current feedback?

rcastle1, 2019-02-08:
Closing. Circuits added to LV_IO PCB

Closed 2019-02-08.

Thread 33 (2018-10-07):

TEMPLATE: Pressure Sensor -- Line

rcastle1, 2018-10-07:
### Purpose:
Pressure sensors monitor what the pneumatics system is doing. They are critical for safety as pressure systems can explode.

### Circuit Description:
There are two primary pressure sensor inputs
* 5V
* 24V
There are a few main types of pressure sensor outputs.
* 4-20mA output
* 0-5V
* 0.5-4.5V

Our Pod III Circuit did a nice job of being configurable, as a lot of the time we may need to add in a sensor last minute after a design review and they are fairly difficult to source in these low quantities. I think the main improvement for this circuit will be improved connectors and to think through how we will interface with the sensor. Note that we probably don't need LV_Batt for this.

One improvement that we could possibly make is to have a precision 5 or 24V reference here. Output voltage fluctuates with input voltage to a degree (particularly with higher frequency, lower amplitude noise) so a good twisted pair and a voltage reference would be a nice to have.
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

clendening, 2018-11-01:
Snippet pushed to sensor_list

rcastle1, 2018-11-04:
this could be a good place for "connect by net" instead of "connect by wire" to be implemented. Also not sure if we should be including the breakout connectors in these circuit snippets. Also looks like the footprint for the 3-pin block is from the misc. connectors library and in an uncommitted library.

rcastle1, 2019-02-08:
Closing. Circuit complete

Closed 2019-02-08.

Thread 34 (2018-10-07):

TEMPLATE: LV Battery Monitoring

rcastle1, 2018-10-07:
### Purpose:
While not as dangerous as the high voltage pack, the low voltage battery still needs to be monitored to ensure that it doesn't go into thermal runaway, catch on fire, or operate out of it's datasheet specifications.

### Circuit Description:
* Temperature Monitoring: Thermistor circuit
* Voltage Monitoring: Could go in a few different directions here. Simplest option is a voltage divider, although we could use a battery monitor IC for this.
* Current Monitoring: The INA240A Sensor would be useful for a current measurement. This is basically a voltage measurement across a shunt resistor that gets amplified. The INA240 series can have the gain be 50, 100, 200 I believe. When specing a power resistor for the shunt, you have to make sure that the power rating of the resistor (Given in watts) is greater than the power through the resistor (I^2*R losses)

btobin86, 2018-11-12:
Thermistor resistance and output voltage are representative as variable functions. The resistance value for the fixed resistor in the series was determined by finding the resistance of the thermistor at a T at a midpoint of the stated T operating range (-40 degrees ~ 125 degrees), and then setting it equal to that. I also read, however, that you can set it to the resistance value of R25. I will do testing with this sometime this week to judge the accuracy of the circuit's reading.

rcastle1, 2019-02-08:
Closing

Closed 2019-02-08.

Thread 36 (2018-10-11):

Op Amp Math

rcastle1, 2018-10-11:
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
If anyone wants to do some op-amp math that'd be cool. Need to amplify that output of the NPP pressure sensor to 0-50mV scale to 0 to 3.3V

nat950, 2018-11-01:
I have the Op-Amp math. As long as Rf (R5 in the schematic) is 66 times as large as Rg(R6 in the schematic), an output from 0 - 3.3V should be obtained. A 100 ohm resistor for R6 and 6.6K ohm resistor for R5 may be the easiest way to do this.

vkottler, 2018-11-01:
What thing is going to be sampling `PRESS1_OUT`?

rcastle1, 2019-02-08:
@vkottler Beaglebone Input.

Closing

Closed 2019-02-08.

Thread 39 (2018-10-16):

Pre-Charge Component Library Additions

rcastle1, 2018-10-16:
Comment below when you start working on one of these components and check if off once complete.
Source: https://uwmadison.box.com/s/x3dgq83uid5b81i9zpowtwe9d5qch53k
Schematic Symbol
- [ ] CHSF-250 Fuse
- [ ] 1amp 300 V Fuse
- [ ] Contactor
- [x] S300 YR Diode
- [ ] SPST-NC Relay
- [x] SPST Relay
- [x] DPDT Relay
- [ ] 1k Power Resistor

Footprint
- [ ] CHSF-250 Fuse
- [ ] 1amp 300 V Fuse
- [ ] Contactor
- [ ] S300 YR Diode
- [ ] SPST-NC Relay
- [x] SPST Relay
- [x] DPDT Relay
- [ ] 1k Power Resistor

Ghood08, 2018-10-16:
10/15 I'm starting to work on the s300YR Diode

rcastle1, 2018-10-16:
Looked through a few components and noticed a few things
* https://www.infineon.com/cms/en/product/transistor-diode/diode/chip-diode/sidc161d170h/#!overview This is wafer, not a component that goes on a PCB. See https://en.wikipedia.org/wiki/Die_(integrated_circuit) for more information. I've never spun my own silicon, so that would be cool, but probably not what we're looking for. It also has zero available on Digikey @Ghood08
* BK/GLR-1 Looks like a cartridge that's normally mounted on a panel, rather than a PCB. The datasheet's not loading right now, but check out the suggested mating component. That's usually used on a metal panel for something that needs to be replaced somewhat often, without opening up the rest of the enclosure.
* Be sure to specify the part numbers for CHSF-250 Fuse and the Contactor.
* https://www.digikey.com/product-detail/en/te-connectivity-potter-brumfield-relays/T9GV2L14-12/PB2373-ND/8345133 Is this going to be used from the output of the motor controller? Check out the output voltage of that, I think it's only 3.3 or 5V, so you may need an optocoupler or other method to step up the voltage. Could be fine, depending on how you want to use it.
* https://www.digikey.com/product-detail/en/kemet/EE2-12NU-L/399-10997-1-ND/4506449 I might look for a different package here. This type of lead tends to snap on fairly easily.
* https://www.digikey.com/product-detail/en/ohmite/HS150-1KF/HS1501KF-ND/5306251 Think through how the footprint should look for this component.

yashwani2000, 2018-10-30:
Which branch do I push to? Currently I've saved changes to yashwani2000_training?

yashwani2000, 2018-10-30:
I'm starting to work on the DPDT relay and just updated the sepc'ing sheet, so could you please review the component?

rcastle1, 2019-02-08:
Components added. Closing

Closed 2019-02-08.

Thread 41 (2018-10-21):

Floating Beaglebone Footprint

rcastle1, 2018-10-21:
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
Currently the beaglebone footprint is floating. This isn't great, as we want to know the actual height of the component for cutting holes in the enclosure and determining how much room we have underneath the board so that we know if we're hitting anything.

The task is to take the beaglebone and create an assembly with the beaglebone and the 0.1" pin headers, then export this a a single .stp file (can be done in NX). Note that you need to edit the existing pin headers, as we only have up to 2x16 currently.

Note that if you don't want to learn git, you can just email me the files and I will add to git for you.

SOLIDWORKS file for the beaglebone is located here: https://github.com/badgerloop-software/podiv-altium/blob/libraries/src/lib/stp/BeagleBone%20Black.SLDPRT

Headers are located here: https://github.com/badgerloop-software/podiv-altium/tree/libraries/src/lib/stp

rcastle1, 2018-10-23:
@keving98g update?

rcastle1, 2019-02-08:
Not Resolved. Closing

Closed 2019-02-08.

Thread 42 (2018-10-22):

processor board wrap up

rcastle1, 2018-10-22:
Pressure sensor circuit routing. (I changed the op-amp configuration from a differential amplifier to a two op-amp instrumentation amplifier to reduce component count and increase accuracy over the range of the sensor.)

Make sure that my polygon necks and high current traces are properly sized

Still a few net antennas (unrouted nets) floating around

Design rule check fixes (mostly silkscreen, a couple placement adjustments)

exporting a step file and align this board with the power board to make sure everything lines up ok. Focusing on the top dsub connector and the ethernet jack of the beaglebone.
I'm pretty busy this week, so if anyone wants to do any of that that'd be cool, I probably can't finish it until next weekend.

rcastle1, 2019-02-08:
REVA Board ordered on 2/5/2019 https://github.com/badgerloop-software/podiv-altium/tree/master/board_release/processor/REVA/gerbers

Closed 2019-02-08.

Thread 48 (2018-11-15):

Precharge Initial Issues

rcastle1, 2018-11-15:
Noticing a few issues with the precharge circuit.
* This is just a text string. It has no actual impact on the schematic or layout. You need to use a Net Label and ensure that you are connected to an actual wire. You can do this by trying to drag the Net Label around after you've placed it. If the wires moves along with it, you have a connection, if not, there's no actual electrical connection.

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

A few issues in the following image:
* Net Labels
* if you add an image, please embed the image in the symbol, otherwise it won't appear when anyone else looks at it. A standard symbol like a relay probably doesn't need an image.
* Remove the "-/" in "-/GND" on pin 5 for the relay symbol. You should then make it invisible.
* Add a ? after the designator in the library. If you do that, you go to annotate, it will automatically change the designators from D? to D1 - D12345.
* I don't seem parameters for any of the new components. Please add (at a minimum) Manufacturer, Manufacturer P/N, Digikey P/N, Digikey Link to the parameters section of each component in the schematic library.
* Remove vertical line on pin 8

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

* You can use the standard resistor symbol for this component. doesn't need to be that large on the schmatic.
* Keep things in straight lines when possible.

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

* You will get a compile error when you run DRC on the schematic. Delete this line.
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

How is any of this supposed to be actually connected? This looks like an attempt to make an exact copy of the schematic from last year, but *that will not work* because that was not a PCB and this is. This has no indication of what's a connection on the board and what's a connection with external wiring. Right now all current paths are in the board. There are no headers for anything like power input (LV or HV).

This isn't showing me that we have a good understanding of how this board will actually work. We either need to get to that state or drop this project and go back to an exact copy of last year with external components wired together.

rcastle1, 2019-02-08:
https://github.com/badgerloop-software/podiv-altium/blob/hv_io/src/prj/pdf/hv_io.pdf Last page of this document has an improved circuit

Closed 2019-02-08.

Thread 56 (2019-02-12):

Example Feature Request: Add power Indicator LEDs to LV_IO PCB

rcastle1, 2019-02-12:
**Is your feature request related to a problem? Please describe.**
The low voltage input/output PCB doesn't have an indicator LED, so sometimes it's hard to tell if it's powered on by default.

**Describe the solution you'd like**
Consider adding a Green LED to the 5V rail

**Describe alternatives you've considered**
It's possible to take a voltage measurement, but that's not as easy as looking at the PCB

**Additional context**
HV_IO PCB has this feature.

Closed 2019-03-23.

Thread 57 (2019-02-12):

Example Bug Report: STP files are too large

rcastle1, 2019-02-12:
**Describe the bug**
When exporting STEP files from Altium, the outputs are huge. Each face is exported as it's own solid body.

**To Reproduce**
Steps to reproduce the behavior:
1. Go to any output job file
2. Right Click on the STEP Export and click "Configure"
3. Match these settings
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
4. Close
5. Hit Generate Content
6. Resulting STEP file can be observed to be on the order of 1GB, before even converting from STEP to .prt

**Expected behavior**
A smaller output STEP as a single part file with only one body would allow for easier mechanical integration

**Additional context**
Bug not critical. NX can still open the files, but it's really slow. PCBs will currently be removed from the full pod assembly, and only used for fabrication of the Low Voltage and High Voltage modules.

rcastle1, 2019-03-23:
Removing as this issue can be resolved directly in NX. Could be automated though.

Closed 2019-03-23.

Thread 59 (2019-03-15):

CAN Power

rcastle1, 2019-03-15:
**Describe the bug**
VCC power for the SN65HVD256 (CAN transceiver) is tied to 3.3V, but actually requires 5V. The IC will go into shutdown mode below 4.8V (max threshold).

**Solution**
Perform the following rework:
1. Cut the trace between pad 1 of C1 and the POS3V3 via, indicated via the blue line.
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
2. Deadbug 5V from the nearest point available (POS5V on pin 3 of P10)
3. Cover the exposed via with kapton tape to prevent shorting.

Add any other context about the problem here.
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
* Pin 5 is ok to stay at 3.3V per the datasheet.

rcastle1, 2019-03-15:
Note that this should not require a board spin.

rcastle1, 2019-03-24:
Issue fixed in REVB. REVB required due to incorrect pins on the power connector.
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

rcastle1, 2019-03-24:
5V Reworked on Processor Board REVA 001 for testing.

Closed 2019-03-24.

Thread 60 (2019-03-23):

HV_IO Breakout

rcastle1, 2019-03-23:
@shelby noticed that I (stupidly) didn’t breakout the shutdown circuit lines to the DSub. Issue was resolved by connecting 18 awg wire to the underside of the PTH on the jumper to the PTH on the dsub. This is all just 12V <0.5A to drive the contactor, so this solution should be ok. All wiring is on the bottom side of the board too ;)

@Shelby can you comment with the updated pinout?

If the board is REVed, add breakouts.

<sub>Sent with <a href="http://githawk.com">GitHawk</a></sub>

rcastle1, 2019-03-23:
@dawiggleman ^

dawiggleman, 2019-03-24:
Yes,
Connector J4B:
Pin 13: Inertia Switch +
Pin 14: Inertia Switch -
Pin 17: Master/E-Stop Switch +
Pin 18: Master/ E-Stop Switch -

rcastle1, 2019-03-24:
Thanks. Were you able to test this out? I saw the rework today

rcastle1, 2019-03-24:
Will be resolved in REVB

rcastle1, 2019-04-22:
Board is assembled, in queue for validation.

(this got sidetracked due to other priorities due to reveal. Aiming to have board validated by 4/24)

rcastle1, 2019-06-09:
Rev B functioning as expected.

Closed 2019-06-09.

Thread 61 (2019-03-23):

Processor Connection

rcastle1, 2019-03-23:
Unfortunately, we’ll have to REV the processor board. The pinout for the power board connection was based off of an older branch and is thus wildly incorrect. When power and processor boards are connected, 5, 3.3V and GND are all shorted together.

In the meantime, I added a connection for the 3.3V rail that allows the beaglebone and the rest of the system to be powered off of the barreljack rather than the power board. So CAN, and GPIO can be tested right away. Lv io and hv io can also be tested after I inspect those boards.

I will also resolve the CAN power issue on rev B.

An additional improvement will be to add a jumper to the 3.3V rail so that if we do want to work off of the barrel jack connection we can do so easily.

It was also suggested that we switch the pressure sensor back to I2C. I will see how much re-layout time that will take.

<sub>Sent with <a href="http://githawk.com">GitHawk</a></sub>

rcastle1, 2019-04-22:
Processor REVB populated for both modules.

New CAN circuit based on this guide: https://www.thomas-wedemeyer.de/beaglebone-canbus-python.html appears to solve the CAN/Ethernet dropout issue documented here: https://github.com/badgerloop-software/podiv-altium/issues/65
New Pressure Sensor: I2C pressure sensor, same as pod III
GPIO expander also verified and I2C Bus is functioning.

RevB appears to be a success! No known bugs

Closed 2019-04-22.

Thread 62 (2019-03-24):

Minor Issue: Beaglebone 3D model offset

rcastle1, 2019-03-24:
**Describe the bug**
A clear and concise description of what the bug is.
In the 3D footprint of the beaglebone, the offset if off. This caused the 3D print cutout to be a bit too short and caused us to miss cutting out the USB connector. This was solved by just cutting out more of the slot.  Future versions should add the standoffs to the beaglebone model.

Closed 2019-03-24.

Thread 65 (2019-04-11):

Bug: Ethernet Dropout

rcastle1, 2019-04-11:
Issue: We found that ethernet was dropping out intermittently when the beaglebone was plugged into the low voltage io board and the XSens IMU dev board was plugged into the low voltage IO board. This causes SSHing to fail. For quick monitoring, we are viewing the link light on the switch. In all cases, it will go on for about 10s then turn off. in ~5s if the connection is ok the light will turn back on, and if it's not working it will remain off.

Power: The beaglebone is powered directly from the manufacturer provided 5V wall wart supply. All rails are constant at 5.90 and 3.44V whether the issue is present or not. No rails are shorted out.

Troubleshooting steps:
1) Because this issue was discovered while attempting to bring up the IMU on the I2C bus, we suspected that the issue was because of a problem with I2C. We verified 10k Ohm resistor pull ups on SDA and SCL were popualted and removed all 0Ohm resistors connecting each I2C devices to the bus.
2) We then moved to guess and check, by jumping individual pins from the processor board to the beaglebone. I2C, SPI, UART had no issues connected
3) When connecting CAN RX the issue appears. Below is a scope capture of SYS_RESET and CAN_TX when the issue is *not* present. CH1 is SYS_RESET, CH2 is CAN_TX. CAN_TX goes high approx 22ms before SYS_RESET goes high. CAN_TX logic 1 is at 3.6V.
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

Below is a scope capture of when CAN RX is plugged into the processor board and the beaglebone. Note that CAN_RX logic 1 is at 4.9V after oscillating at ~3.3V for 40ms. Unclear where 4.9V is coming from.  Also note how SYS_RESET rises until the oscillation begins and then falls, only rising fully after the CAN_RX  signal goes high.
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

What we don't understand:
1) Why did this issue get exposed when bringing up a (to our knowledge) unrelated system?
2) Why were we able to use CAN and read from BMS and Motor controller for ~2 weeks without this issue coming up?

Next proposed steps:
1) Remove the CAN transceiver and see if the issue occurs with all LVIO and XSENS boards plugged in.
2) Put a fresh CAN transceiver on the board

Related parts: https://www.microchip.com/wwwproducts/en/MCP2561

rcastle1, 2019-04-12:
Confirmed that the issue does not occur when the transceiver is not populated

rcastle1, 2019-04-12:
Removed D1 and D2 to reduce variables.
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

rcastle1, 2019-04-12:
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
Updated RX waveform on powerup after replacing transceiver. No oscillations, but still doesn't have a monatomic power on sequence.

rcastle1, 2019-04-12:
Tried connecting VDD to 3.3V instead of 5. The Ethernet dropout issue goes away, but CAN is unable to be read from the BMS or motor controller. I put a scope on CANL and it was super noisy.

The current theory is that the 4.9V output on CANRX is too much for the 3.3V pins on the Beaglebone. Pod III Navigation PCB also outputs 4.9V at CANRX so it's a design flaw. The MCP2561 datasheet is a little misleading if you don't read it super carefully as it says it's compatible with 1.8-5V MCU systems, however, that range is achieved by the MCP2562 transceiver using the VIO pin. For the MCP2561, VIO is tied to VDD. So we would basically need VDD to be 3.3V to not damage the Beaglebone, but a VDD of 3.3V isn't sufficient to overcome the internal Under Voltage Lockout Protection.

Ordered some SN65HVD231 which should be in Saturday. I can install these and remote work can happen. These are designed to have a 3.3V input. Following the non-isolated CAN design for Beaglebone from this site. https://www.thomas-wedemeyer.de/beaglebone-canbus-python.html

rcastle1, 2019-04-14:
It's alive! Looks like changing the transceiver fixed the Ethernet Dropout issue without destroying the CAN interface.
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

rcastle1, 2019-04-14:
https://uwmadison.box.com/s/1mu59td1yyi7hdjs0yp8ii201jvwkds3 Here's a really exciting and well edited video demonstrating functionality

rcastle1, 2019-04-22:
One note on this, pin 3 requires a 3.3V input, rather than a 5V input, so that requires rework, which is currently applied to the active processor boards.

Closed 2019-04-14.

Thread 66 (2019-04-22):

RTC

rcastle1, 2019-04-22:
**Is your feature request related to a problem? Please describe.**
The beaglebone requires on external network connection to avoid clock screw errors when building code. Development in crunch time could possibly become pretty tricky (like in the middle of a parking lot). Additionally, without a RTC we are unable to send timestamps on data, so we don't know our latency with the connection to the pod.

Originally requested by @ezraboley via Slack

**Describe the solution you'd like**
* If any board are rev'ed, add a simple RTC circuit.
* In the meantime, a breakout board like this https://www.adafruit.com/product/3013 can be attached / soldered to the I2C bus.

**Describe alternatives you've considered**
* Not having a RTC. This isn't mission critical, but will be very useful in crunch time

**Additional context**
Add any other context or screenshots about the feature request here.
Links: https://saintgimp.org/2017/11/05/add-a-real-time-clock-to-a-beaglebone-black/
https://cdn-learn.adafruit.com/downloads/pdf/adding-a-real-time-clock-to-beaglebone-black.pdf

rcastle1, 2019-06-09:
Installed in LVIO module box.

Closed 2019-06-09.

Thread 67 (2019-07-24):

Upgrade to a 12-bit ADC

ezraboley, 2019-07-24:
**Is your feature request related to a problem? Please describe.**
Our resolution is preventing us from getting more accurate readings from sensors using our ADCs

**Describe the solution you'd like**
Replace the current 8-bit ADC with a 12-bit IC (ideally if there exists one with the same footprint)

**Describe alternatives you've considered**
A 10 bit ADC, or reworking the footprint on the next rev.

**Additional context**
Also need to do something about the wild Vref line

rcastle1, 2019-07-24:
Agreed. I think the power distribution at the board level should be reference VBus with LDOs just before all of the sensitive analog circuitry. You can get precision reference voltage ICs as well. Additionally, utilize hardware low pass filters

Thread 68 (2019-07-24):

Add a watchdog timer to the processor board

ezraboley, 2019-07-24:
**Is your feature request related to a problem? Please describe.**
Allows for a board to recover if it is stuck in an undefined state. Will override previously discussed hacky solutions to this problem (e.g. LV mod crashing)

**Describe the solution you'd like**
By adding a watchdog timer that is able to reset the LV or HV modules, both will be protected in the case of a crash

**Describe alternatives you've considered**
We discussed some hacky alternatives but they all involve silly amounts of work.

**Additional context**
Pretty much a must for any embedded platform

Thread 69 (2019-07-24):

Add back ambient pressure sensor

ezraboley, 2019-07-24:
**Describe the bug**
@keving98g and I saw weird, unexplained behavior on the I2C bus when the pressure sensor on the Rev B processor board was connected. This was never explained, and we just removed it due to time constraints, but it seems like a pertinent thing to investigate while we are planning a new Rev.

**To Reproduce**
Steps to reproduce the behavior:
1. Make sure U3, R5, and R6 are all placed, putting the pressure sensor on the bus
2. Run `i2cdetect -r -y 2` to see if it is on the bus
3. Run the previous command multiple times in a row and you should see it appear on and off the bus, or crash the bus altogether.

**Expected behavior**
It should read the pressure.

**Screenshots**
None

**Desktop (please complete the following information):**
 - OS: Debian

rcastle1, 2019-07-24:
Definitely agree we should investigate the I2C error, as it also occurred with the addition of the RTC.

There are other, possibly cheaper, options for reading pressure like the analog voltage output sensor we had on the REVA processor.

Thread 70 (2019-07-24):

Fix floating reset pins in next rev

ezraboley, 2019-07-24:
**Describe the bug**
The MCP23017 reset pins have been left floating and need to be tied to 5V in the next Rev

**Expected behavior**
These pins are active low and as such must be tied high

rcastle1, 2019-07-24:
With some logic level shifting, we could have these be controlled directly by the beaglebone(s), rather than just tying them high or through a pull up. That would allow for the reset behavior if one module goes down as expected.

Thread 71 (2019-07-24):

Add an RTC to the processor board

ezraboley, 2019-07-24:
**Is your feature request related to a problem? Please describe.**
When disconnected, we have no way of telling the time. This is both inconvenient (running make) and potentially problematic (e.g. disjointed logging).

**Describe the solution you'd like**
Add an RTC (along with a coin cell battery) to the next Rev

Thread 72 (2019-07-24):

Investigate Connector Alternative

rcastle1, 2019-07-24:
**Describe the bug**
The D-Sub connectors were ok for pod IV, but had several issues.
1. Locking feature was not a part of the mating process. There isn't a positive locking feature on the D-Subs, you have to screw in the backshell. That made it very difficult in some of the hard to reach portions of the pod to connect or disconnect a harness. Furthermore, we wasted multilpe hours debugging just to find that a connector was plugged in, but not plugged in all of the way.
2. The solder cup, again, worked well and no part is usually a good part, however, there were multiple occasions in which the solder connection was poor, which drove us to debug for hours, just to have the issue obscured by a backshell.
3. Connection to large gauge wiring was very poor on the DSubs. Difficult to distribute power (12AWG cable) to the required D-SUB pins.

**Connector Requirements**
1. Locking feature as part of the mating process
2. Backshells or strain relief that is easy on-off
3. Board-to-wire connector, right angle options
4. Relatively high density or at least high pin count (up to 25 or 50 pins)
5. Automotive grade?
6. Rated for power distribution

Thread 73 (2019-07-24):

Switch to all 0805 or larger packages.

rcastle1, 2019-07-24:
**Describe the bug**
Hubris. Hubris is the bug. Just because one can solder down to 0402s, doesn't mean one should, especially because our boards are so big anyway. We ran into so many issues of a resistor not being soldered correctly and re-soldering it vertically on the pod was never an ideal rework station.

**Resolusion**
Next Rev of PCBs should use at least 0805s and should the 0402 and 0603 resistors should be deleted from future libraries.

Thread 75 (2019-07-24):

Update READMEs

rcastle1, 2019-07-24:
**Describe the bug**
Readmes are very out of date. Update and get a couple of overview videos before the start of the school year.

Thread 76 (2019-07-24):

Harness Verification

btobin86, 2019-07-24:
We ran into a few issues where having to troubleshoot and rework harnesses ate up perhaps some unnecessary time. In cases like the resolver harness where there were a few errors, hopefully a second pair of eyes and teams like electrical reliability can help mitigate these problems. Other times, when the harnesses were just physically getting in the way (limit switch harnesses, etc.), perhaps we just dedicate slightly more time planning how things be wired or consulting w/ the mechanical team (that being said, I believe it was said that this year's harnessing was still a lot cleaner than it had been before)

rcastle1, 2019-07-27:
To clean up harnessing, I think there are three primary areas to improve
* High Voltage Wiring
     * High voltage: high current wiring was pretty clean, and the mistake of having the motor connections on the opposite side actually worked well for us. The biggest area of improvement would be to move the battery pack location so that the manual service disconnect requiring less or even no wiring.
     * Precharge Circuit: Internal box wiring was ok, but the DSUBs clearly weren't the right connector. The solder cup connection to the dsub was pretty bad on the panel mount side, especially with high voltage present on those lines. In addition, there was no enforced polarity, which could lead to plugging in the wrong cable.  Pod V should consider incorporating the contactors, high current fuse and precharge resistors onto a single, isolated PCB that's incorporated in the battery pack.
     * BMS Wiring: We didn't have any actual connectivity issues, except that one thermistor coming off of the breakout board, but that was pretty much it. I think the big improvement for next pod would be to incorporate the BMS directly on the pack, similar to how we want to include the precharge circuit better than how the contactor box was done.
     * Motor controller: We definitely need to figure out a better way to pass wires through the pressure vessel than the current setup. We could have lost hours and hours if one of those (jank) connections on the LV feedthroughs came undone. Also consider breaking out all of the motor controller connections, even if we might not use them.
* Low Voltage
     * Power Distribution: DSUBs were not a great connector for power distribution to PCBs. Connection to the LV batteries were OK, and they didn't seem to have an issue with the buckle and powerpole connection, so that could be reused. Consider moving the LV batteries to allow for better access to the electrical boxes
     * The huge bundle going down the starboard side for pressure sensors and solenoids should be replaced with a single, shielded UART/USART/CAN/Misc. Protocol cable and power. An IO PCB that takes in commands to actuate the various valves and constantly spits out pressure sensor and solenoid feedback information could greatly reduce wiring, improve signal integrity. It's also a lot easier to debug a 1ft harness than it is to debug a 10ft harness.
     * Isolation between HV and LV harnessing was pretty good. Removing the HV connection between the HVIO and contactor box would be the most clear improvement.
     * Battery Protection Box: Could be re-done. It was so tight the wiring wasn't great, and DSUBs were again, not a great choice. It would also be good to incorporate power monitoring directly

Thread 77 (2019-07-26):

Charge output/functionality on HVIO,

dawiggleman, 2019-07-26:
Problem:
The opto-isolator that was turned on to allow for 12V to power the contactor inside the charging box could not source enough current to drive the relay. Instead, we took the output of the shutdown circuit and made a harness to drive the relay if the shutdown circuit was completed.

Solution:
Add an additional net off of the shutdown circuit output to an on-board connector that drive the charge contactor without having to remove the main contactor box drive harness.

Problem:
In order to close the shutdown circuit without  controls intervention, 5V needed to be manually jumped with a wire to act as "MCU latch" on the shutdown circuit. Not ideal.

Solution:
Add a simple push-button that when pushed, connects 5V with MCU latch net.

rcastle1, 2019-07-26:
it would be good to have the option for these config inputs to be software controlled in addition to manual switches. this is the same for the charge/discharge/balance enable switches as well.

Ideally, the full pod would be on an monitoring telemetry during charging, but in California it's likely that charging will occur late at night and the software folks should use the sleep.

dawiggleman, 2019-10-09:
Let's remember to add multipurpose inputs/outputs from BMS in main BMS connector- output can be configured to be activated if temperature goes above a certain temperature which would be nice to have in addition to discharge enablesignal

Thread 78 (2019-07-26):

HV wiring

dawiggleman, 2019-07-26:
Problem:
The high voltage wiring between the contactor box and the motor controller was convoluted and excessive, when a more direct path probably would have been possible with more foresight. Optimizing (shortening) this route will save in both efficiency and power delivered to the motor controller, as well as minimizing locations for a potential isolation failure.

Solution:
Integrate contactor box into battery pack design sooner in design for more direct HV wiring.

rcastle1, 2019-07-26:
We could also consider moving the location of the battery box. where is is now basically requires an excessive amount of wiring to get to the high voltage disconnect (which has to be accessible on the outside of the pod).

Integrating the contactors, BMS and thermistors in a single battery container would be really clean as well

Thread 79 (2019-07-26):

HV Indicator light on High Side Contactor

dawiggleman, 2019-07-26:
Problem:
The HV indicator light turned on if the high side contactor was closed, but the low side contactor was not closed. This was due to the pre-charge connection on the low side contactor being attached to the battery - side of the contactor, rather than the side that received battery - when the contactor was closed. Changing this side appeared to give an undervoltage fault to the motor controller, but upon further investivation after switching back to the original configuration, one of the precharge harnesses was loose.

Solution:
Place HV_GND net ring terminal on the side of the low side contactor that normally does not attach to battery -.

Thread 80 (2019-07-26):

Motor controller tries to precharge upon power up

dawiggleman, 2019-07-26:
Problem:

The motor controller attempts to precharge the motor controller by driving precharge relays upon low voltage power up. This appears to be the behavior of the controller if a certain pin is not tied low, and/or the controller is operating in VSM mode.

Solution:
High voltage lead @wyattdvorak investigate which pin needs to be tied low prevent this behavior, and make this connection the next time the motor controller is accessible.

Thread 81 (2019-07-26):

Precharge Circuit PCB

rcastle1, 2019-07-26:
**Is your feature request related to a problem? Please describe.**
Wiring in the contactor box was pretty messy, and had high and low voltage harnessing within less than an inch of each other. Investigate creating a precharge PCB that has these contactors,  fuse and power resistors and relays integrated into the single PCB. This will provide better isolation between high and low voltage, as well as reduce wiring and connectors.

**Describe the solution you'd like**
Create a precharge PCB.

**Describe alternatives you've considered**
Separate contactor box, disconnect, etc. is fine, just not clean.

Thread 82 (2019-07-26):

Investigate Motor Controller Vacuum Compatibility

rcastle1, 2019-07-26:
**Is your feature request related to a problem? Please describe.**
The motor controller hasn't been tested in the vacuum because we are concerned it will arc. We should investigate sealing the controller and testing the controller in a vacuum for an extended period of time. (2 hours, especially if the tunnel is 10km now).

We have always been very concerned we would break the controller if we use it in a vacuum and it's expensive. But a pressure vessel just for the controller is likely just as expensive as the controller itself.

**Describe the solution you'd like**
Run a test with the controller in the vacuum.

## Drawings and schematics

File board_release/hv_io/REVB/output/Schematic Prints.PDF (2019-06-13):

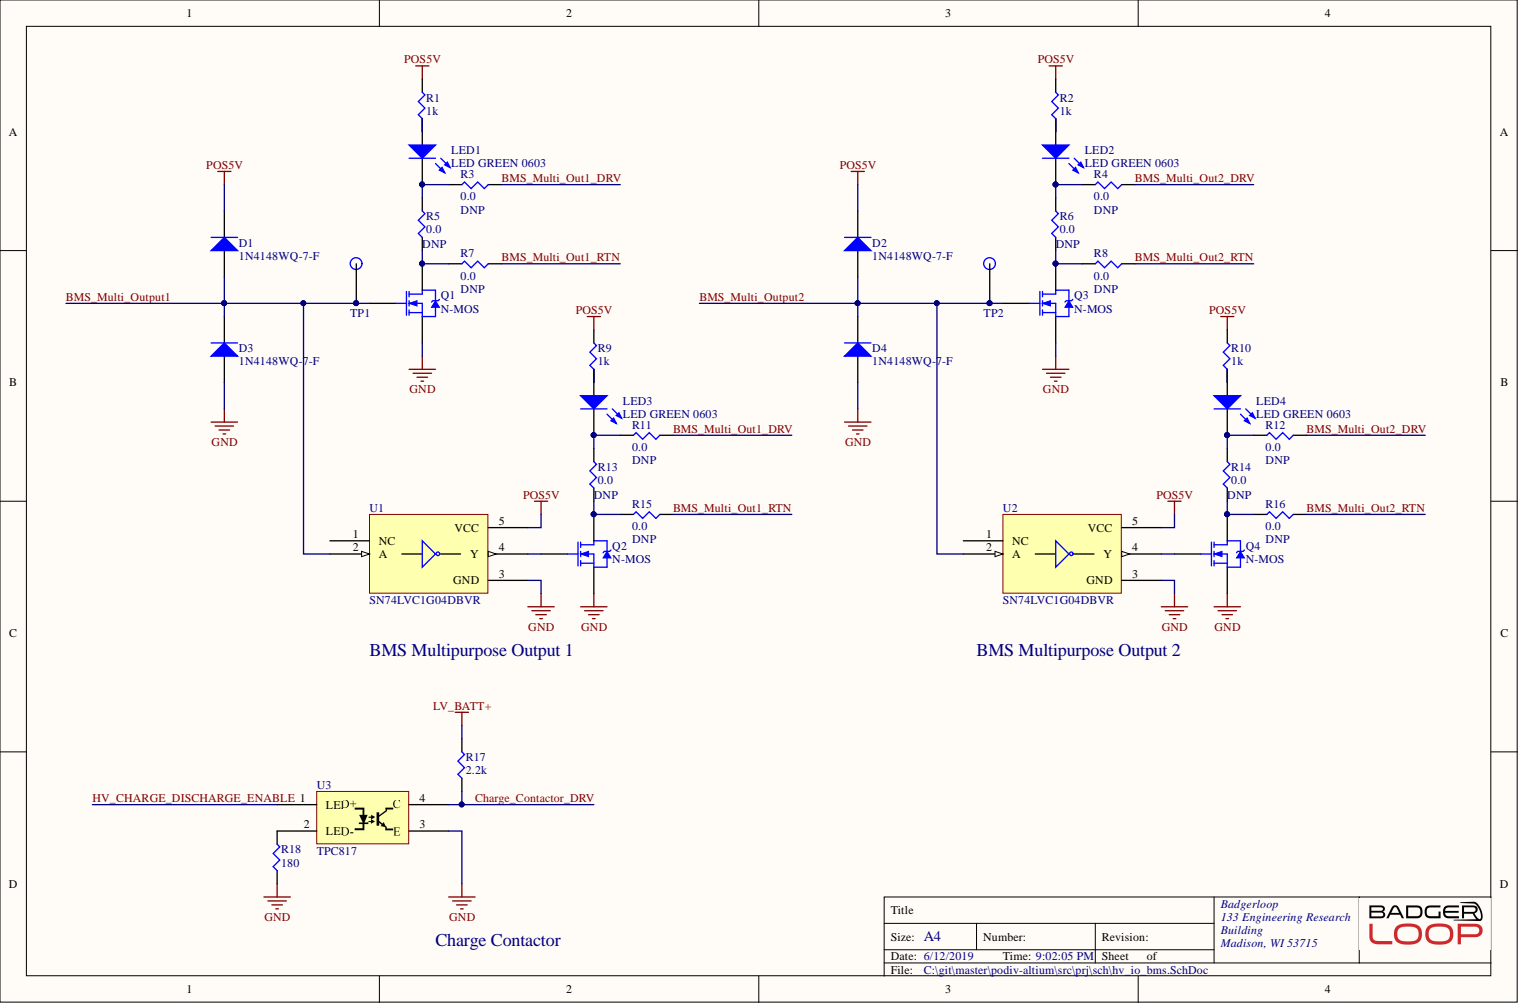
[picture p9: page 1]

Title | Badgerloop 133 Engineering Research Building Madison, WI 53715

Size: A4 | Number: | Revision:
Date: 6/12/2019 Time: 9:02:05 PM | | Sheet of

C:\git\master\podiv-altium\src\prj\sch\hv_io_bms.SchDoc

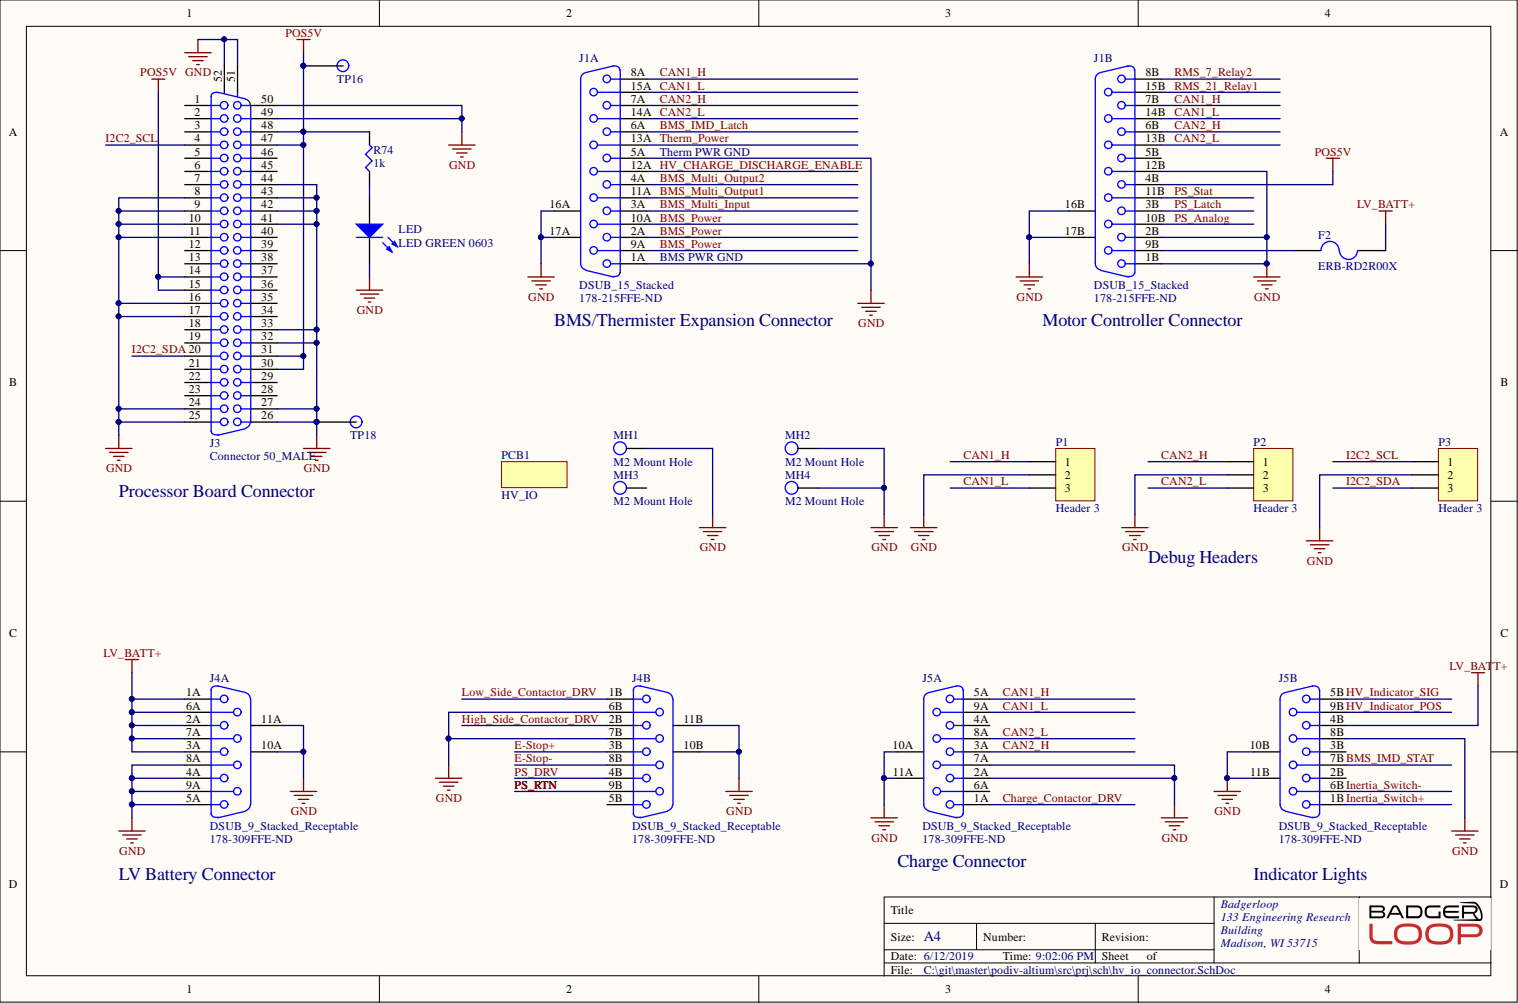
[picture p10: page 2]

4A
9A
5A

C:\git\master\podiv-altium\src\prj\sch\hv_io_connector.SchDoc

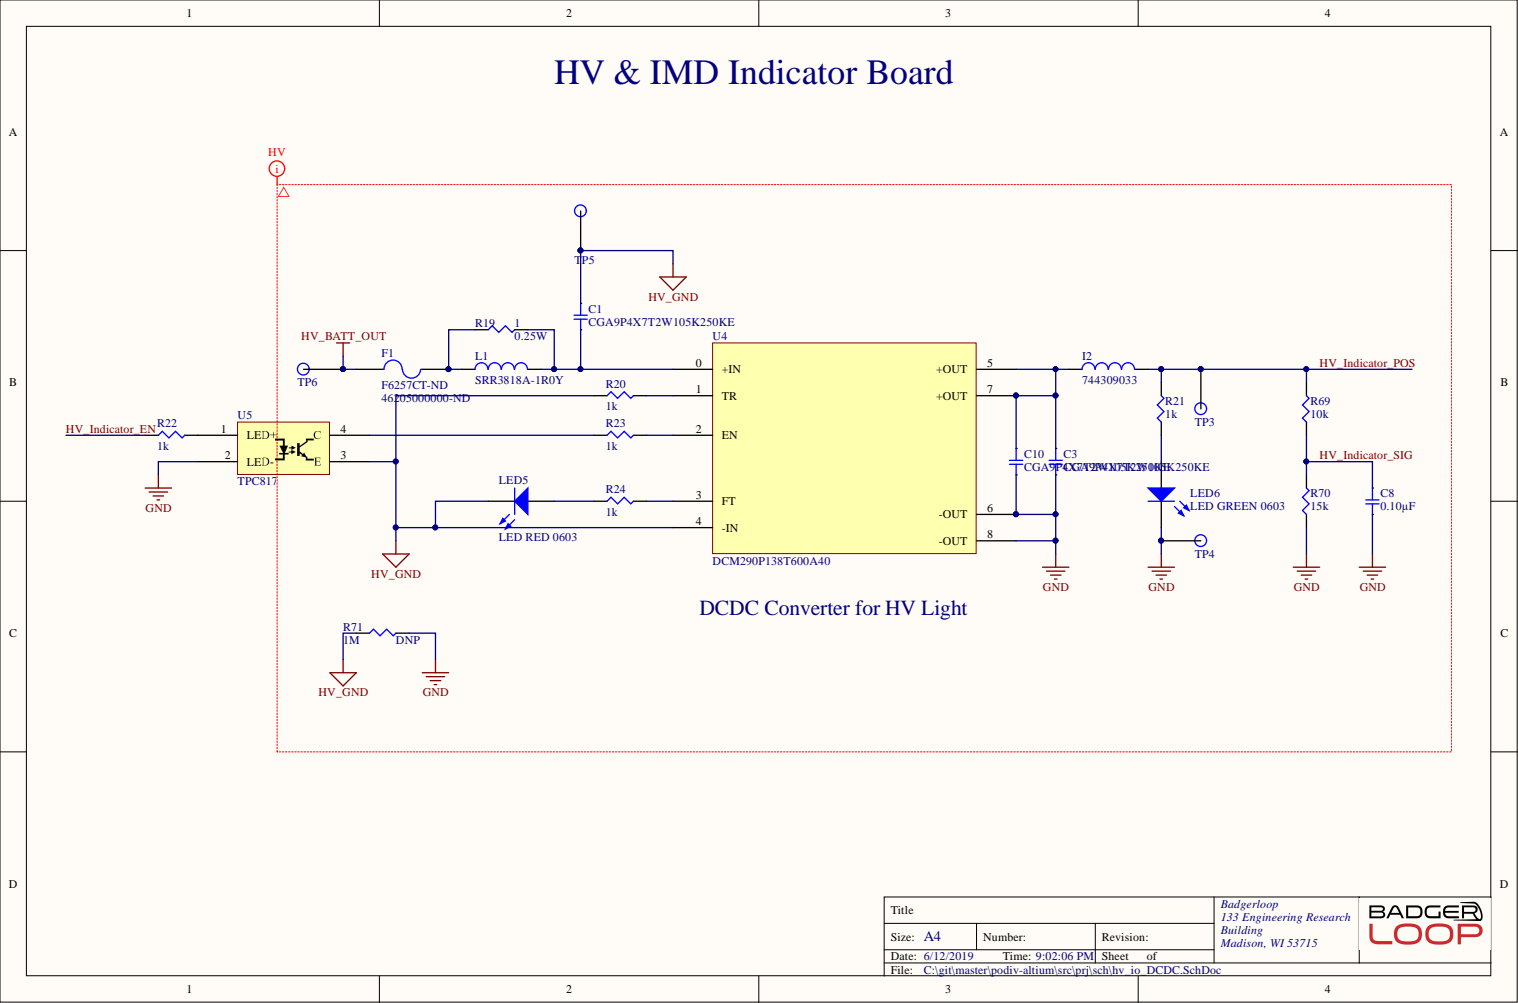
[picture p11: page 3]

HV & IMD Indicator Board

DCDC Converter for HV Light

C:\git\master\podiv-altium\src\prj\sch\hv_io_DCDC.SchDoc

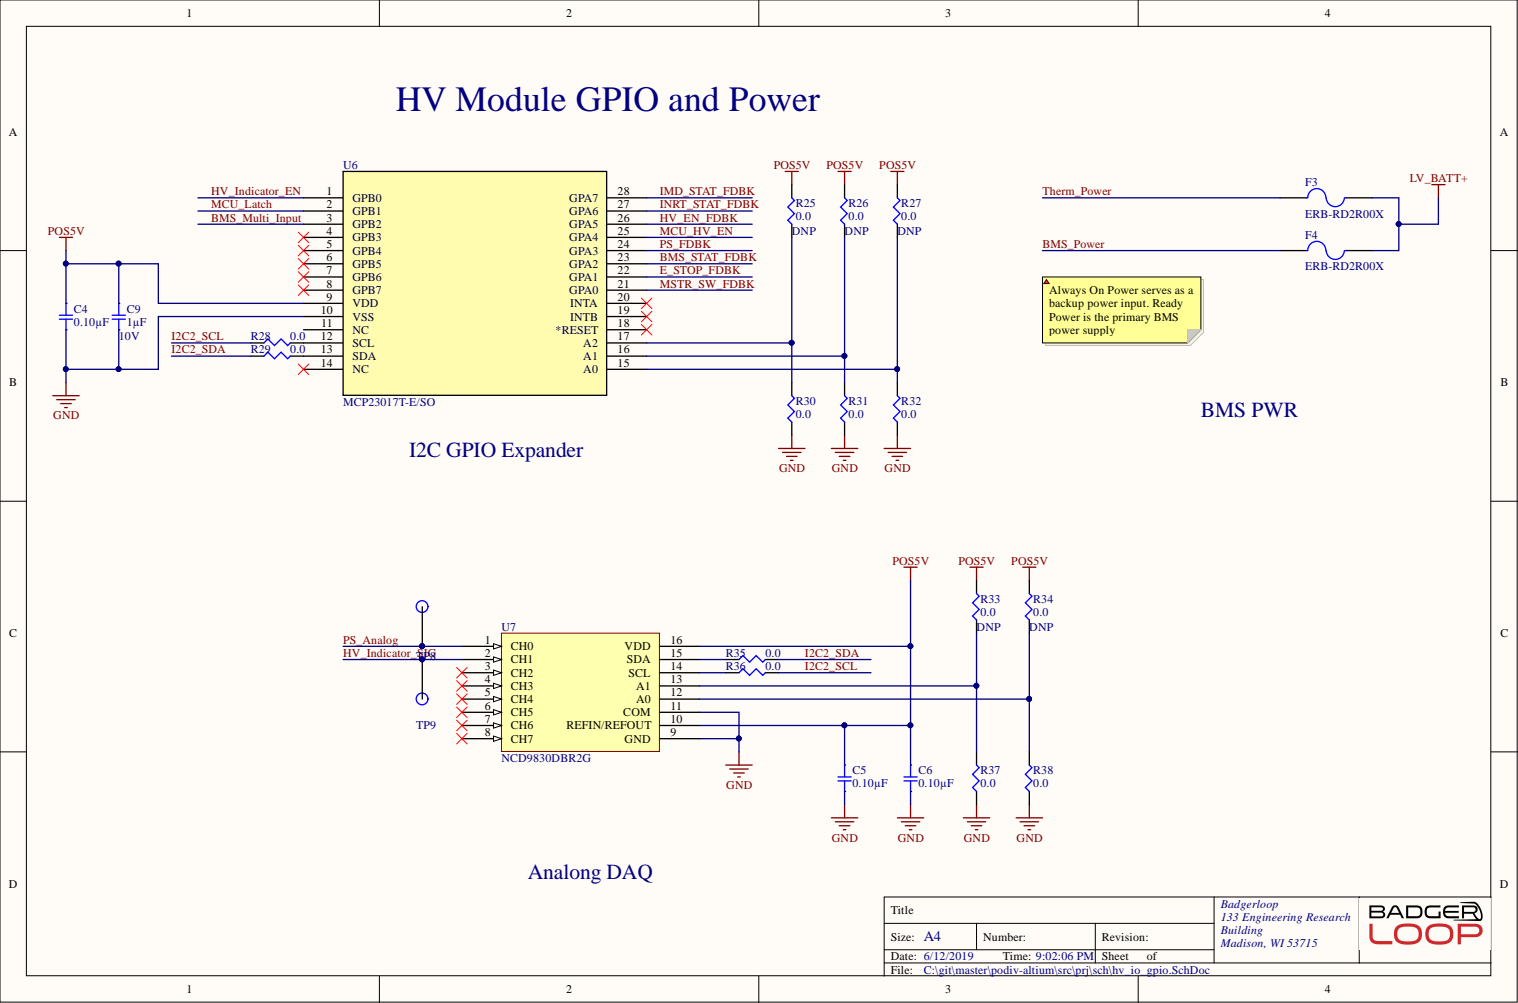
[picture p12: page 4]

HV Module GPIO and Power

Always On Power serves as a
backup power input. Ready
Power is the primary BMS
power supply

C:\git\master\podiv-altium\src\prj\sch\hv_io_gpio.SchDoc

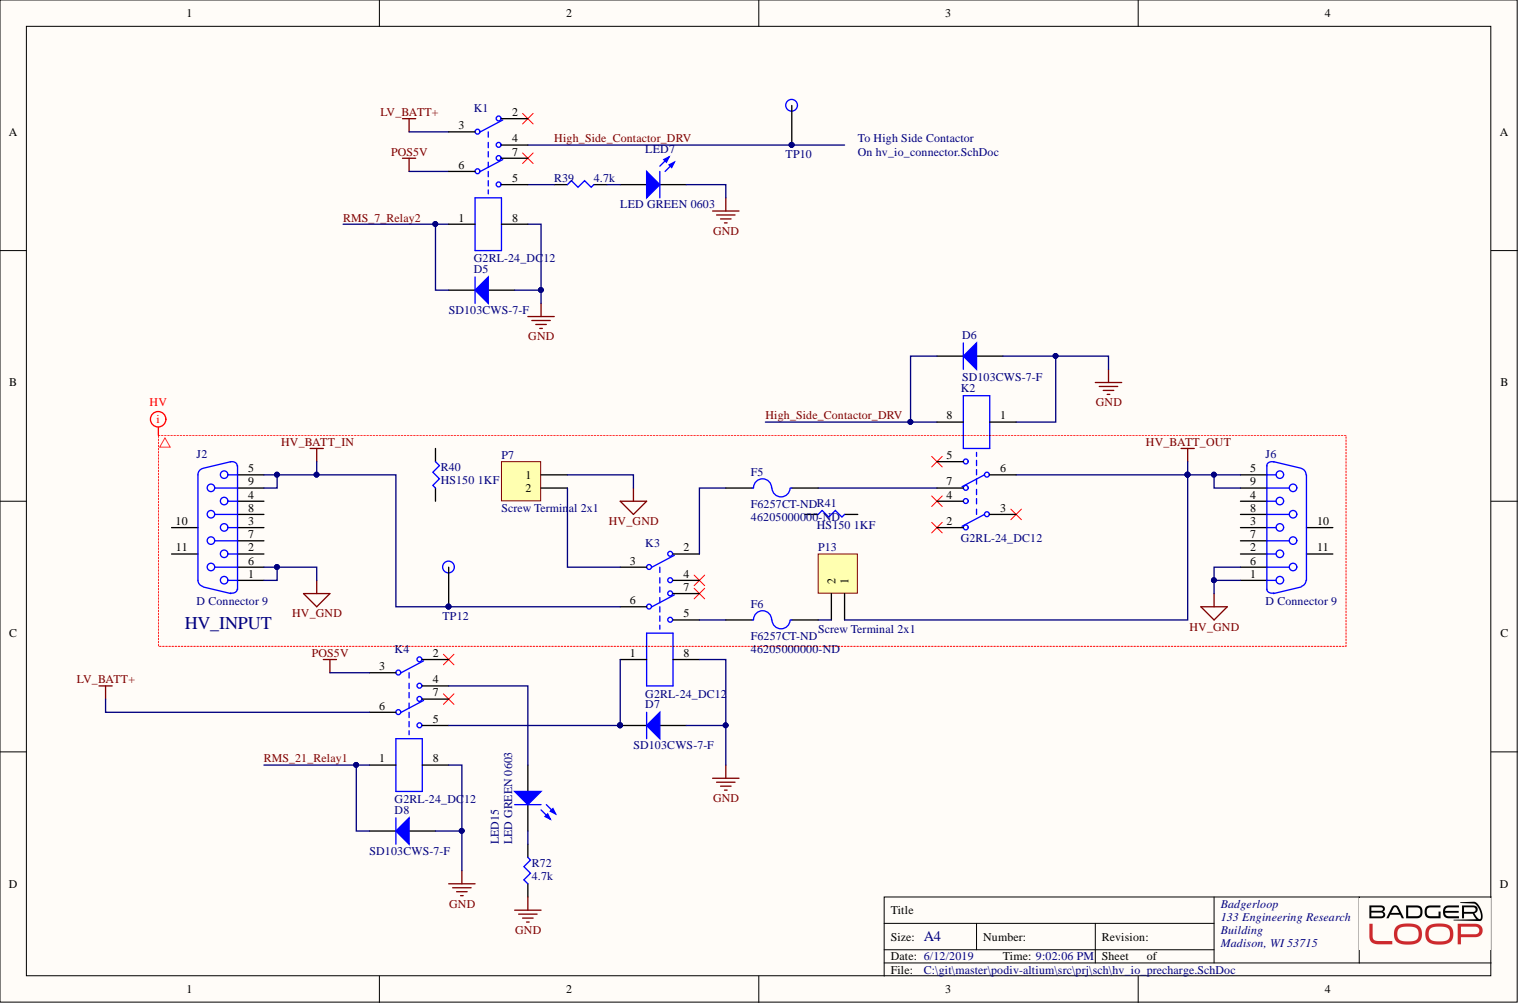
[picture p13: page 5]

To High Side Contactor
On hv_io_connector.SchDoc

C:\git\master\podiv-altium\src\prj\sch\hv_io_precharge.SchDoc

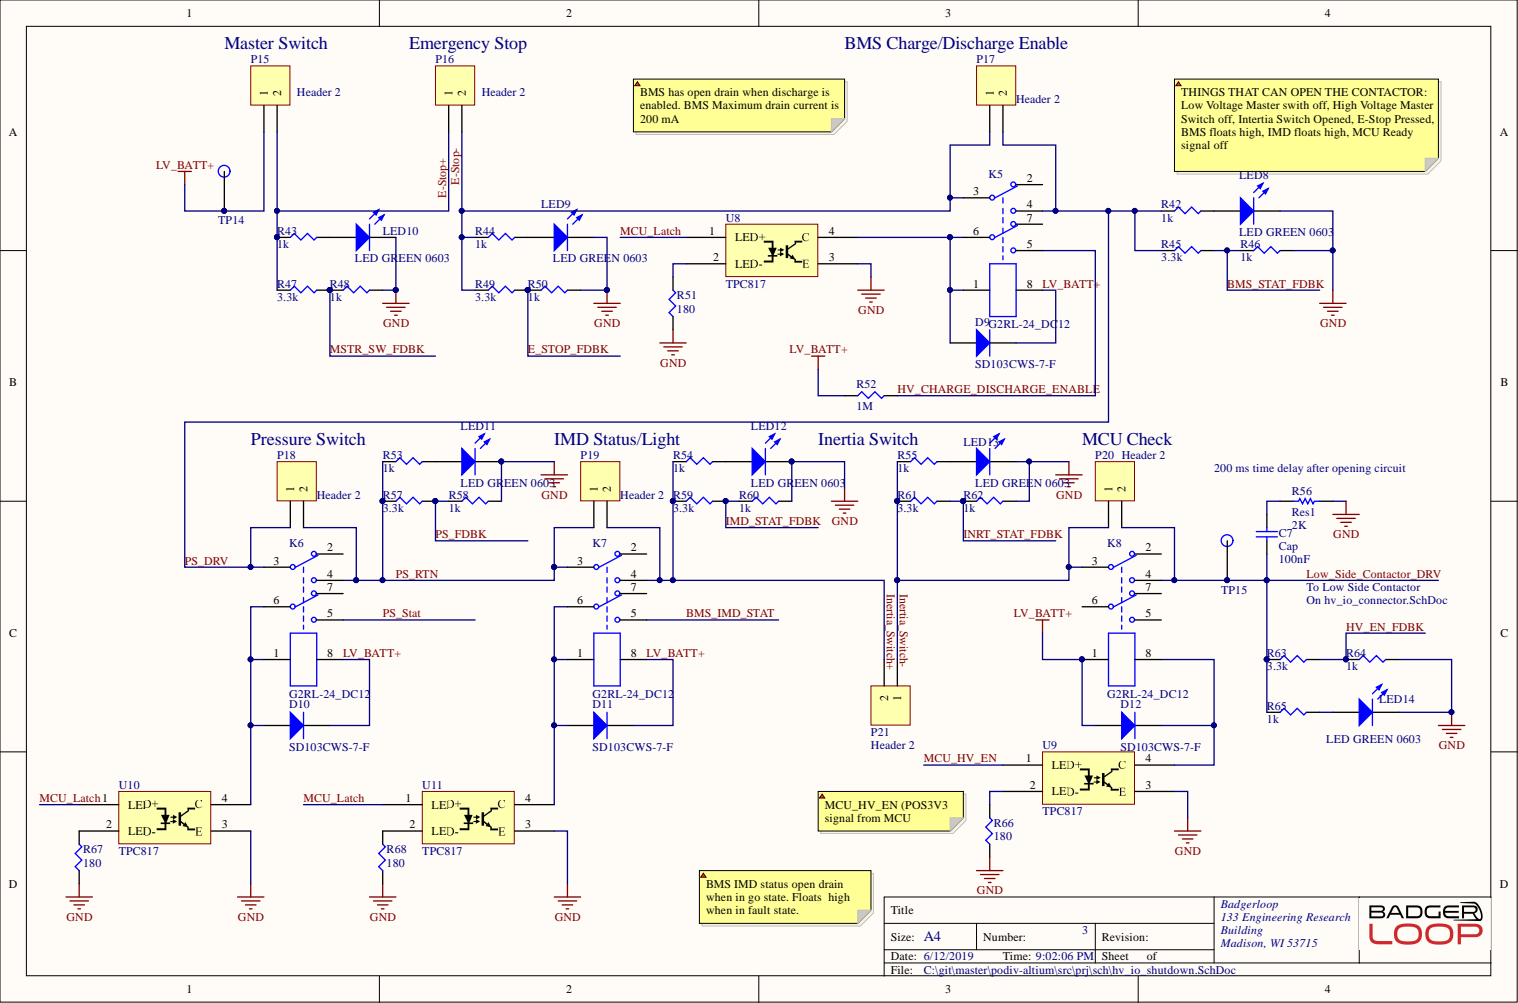
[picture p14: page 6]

BMS has open drain when discharge is
enabled. BMS Maximum drain current is

THINGS THAT CAN OPEN THE CONTACTOR:
Low Voltage Master swith off, High Voltage Master
Switch off, Intertia Switch Opened, E-Stop Pressed,
BMS floats high, IMD floats high, MCU Ready
signal off

200 ms time delay after opening circuit

BMS IMD status open drain
when in go state. Floats high
when in fault state.

C:\git\master\podiv-altium\src\prj\sch\hv_io_shutdown.SchDoc

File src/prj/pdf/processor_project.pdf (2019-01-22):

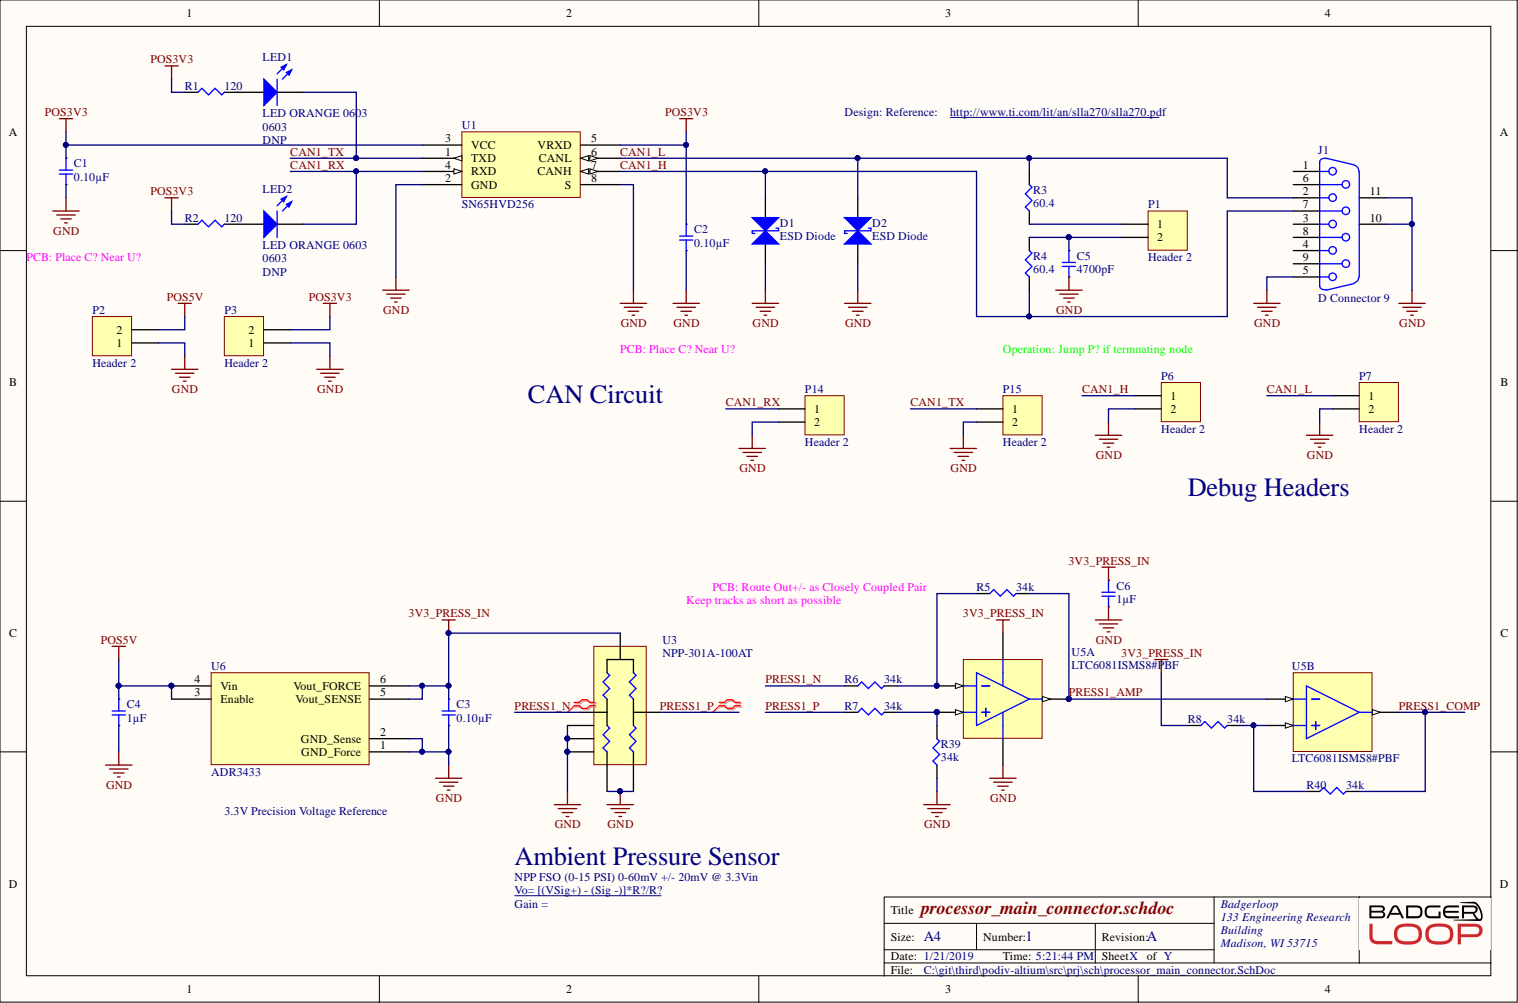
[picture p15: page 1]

http://www.ti.com/lit/an/slla270/slla270.pdf

CAN1_RX | RXD 4 | | CAN1_H | R3

GND 2 | | | 6 2

PCB: Route Out+/- as Closely Coupled Pair
Keep tracks as short as possible

processor_main_connector.schdoc Title | Badgerloop 133 Engineering Research Building Madison, WI 53715

Size: A4 | Number: 1 | Revision: A
Date: 1/21/2019 Time: 5:21:44 PM | | Sheet X of Y

C:\git\third\podiv-altium\src\prj\sch\processor_main_connector.SchDoc

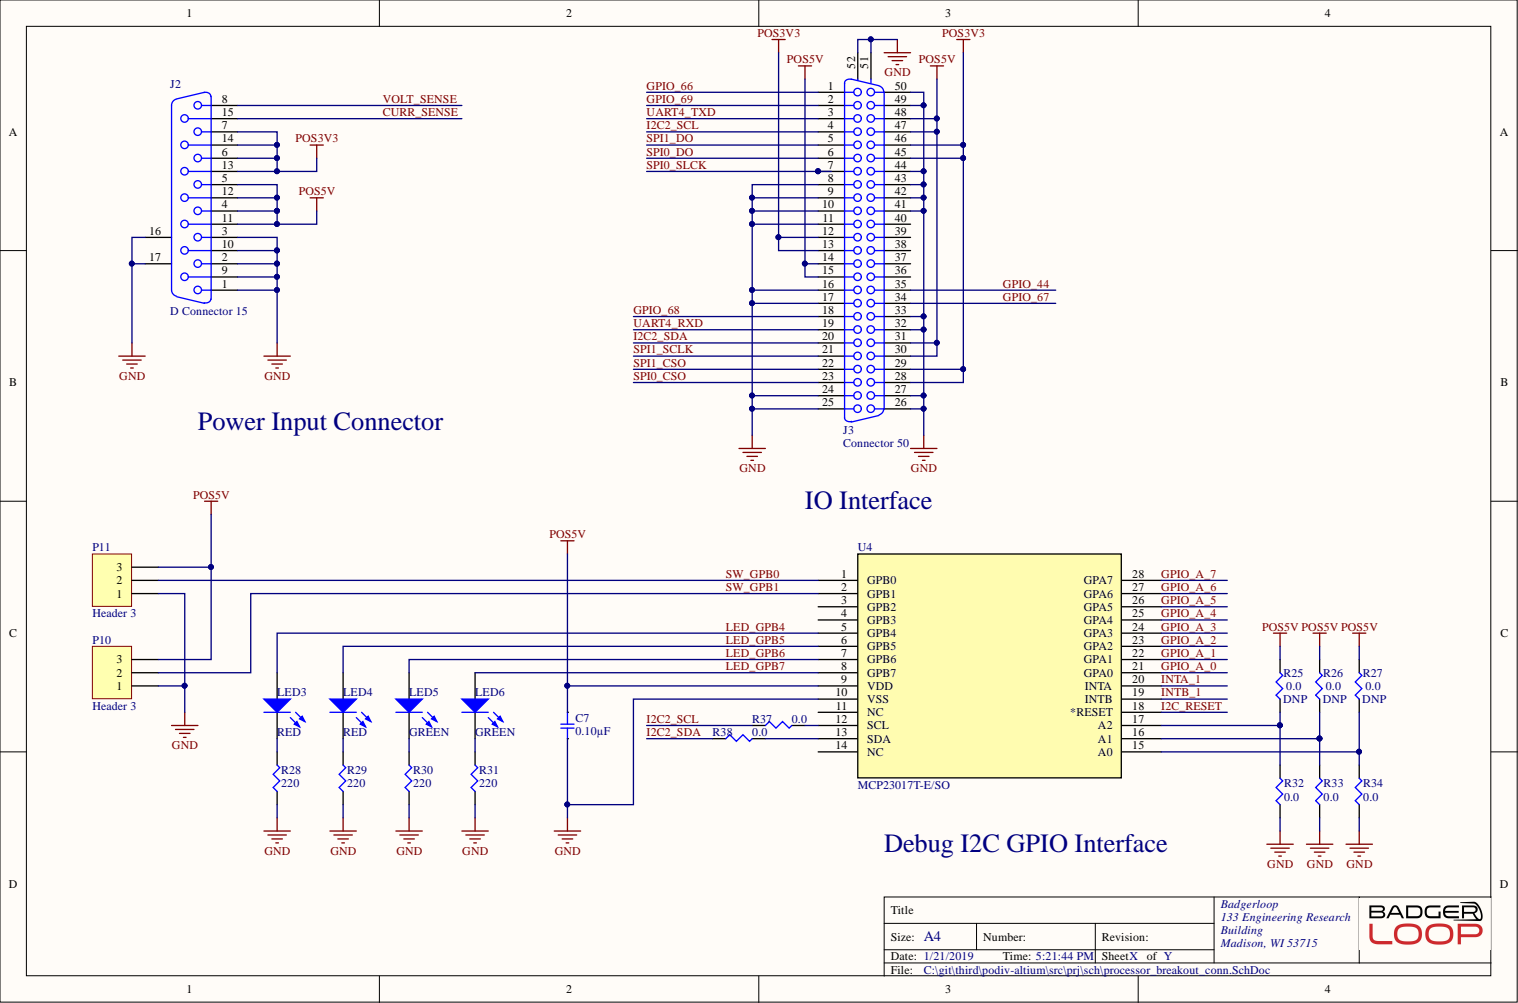
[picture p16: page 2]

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
SW _ GPB1 | 2
L E D _ GPB4 | 3

L E D _ GPB5 | 6
L E D _ GPB6 | 7
L E D _ GPB7 | 8

T i t l e | B a dger l o op 1 3 3 E n g i neer i n g Resea rch B u i l d i n g Ma d i s o n, WI 5

Size: A | N umber: | Rev i s i o n :

/ / T ime: : : 4 PM | | Sheet o f Y

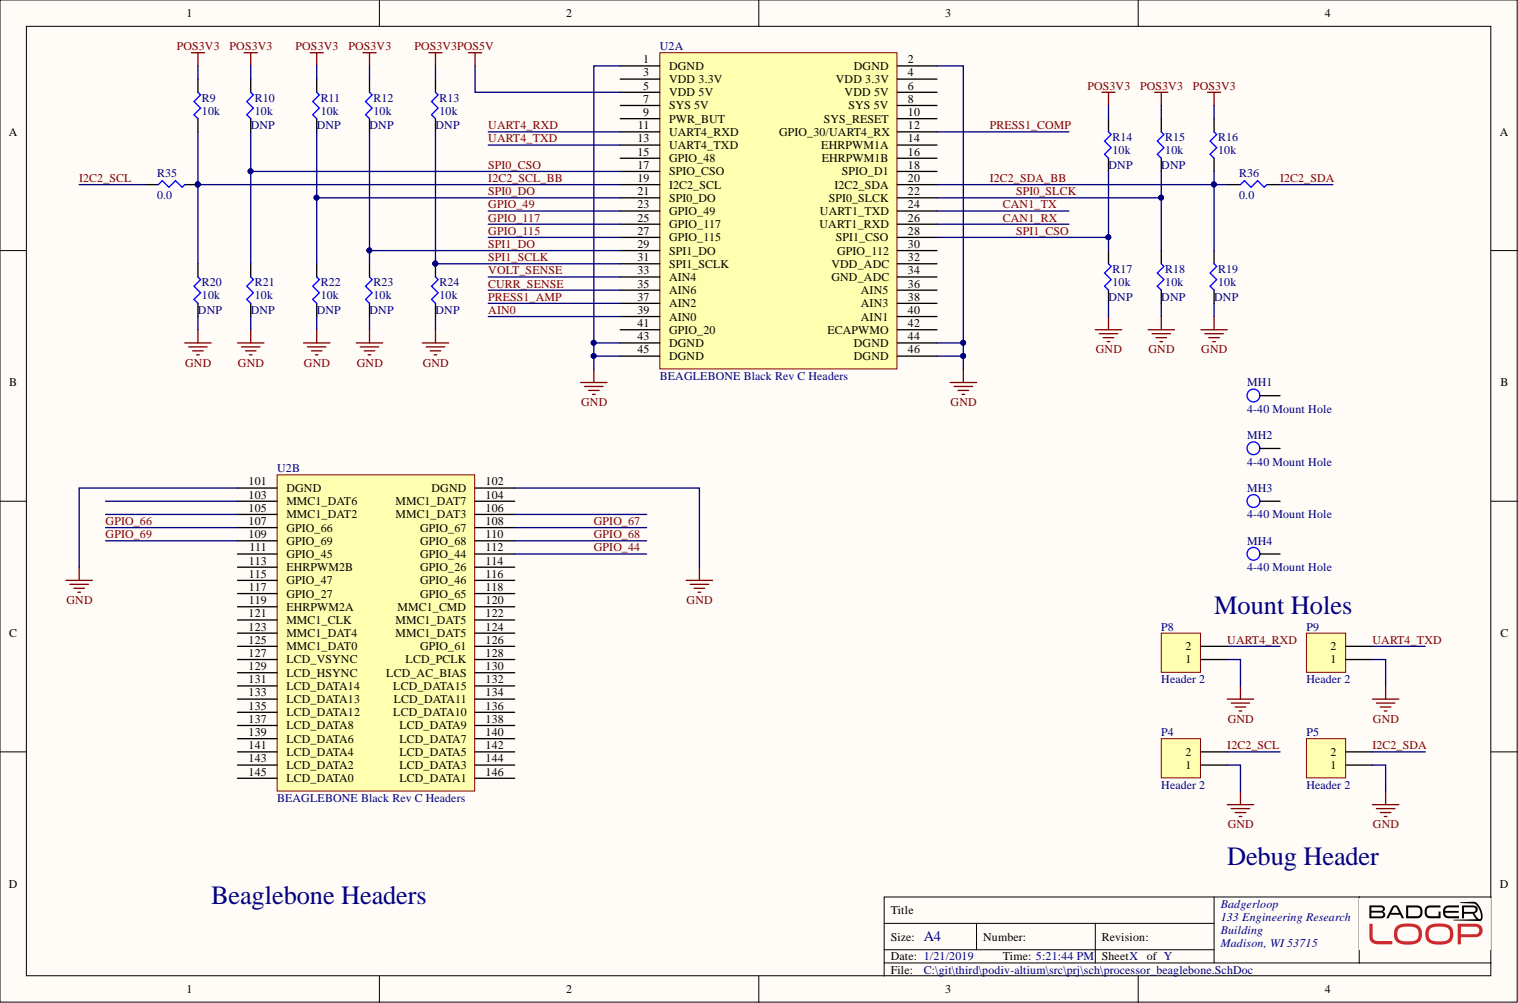
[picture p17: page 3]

UART4_TXD SPI0_CSO

SPI0_DO | I2C2_SDA_BB R35

SPI0_SLCK
GPIO_49 GPIO_117 GPIO_115 SPI1_DO | CAN1_TX CAN1_RX SPI1_CSO

BEAGLEBONE Black Rev C Headers

Title | Badgerloop 133 Engineering Research Building Madison, WI 53715

Size: A4 | Number: | Revision:
1/21/2019 Time: 5:21:44 PM | | Sheet of Y

C:\git\third\podiv-altium\src\prj\sch\processor_beaglebone.SchDoc

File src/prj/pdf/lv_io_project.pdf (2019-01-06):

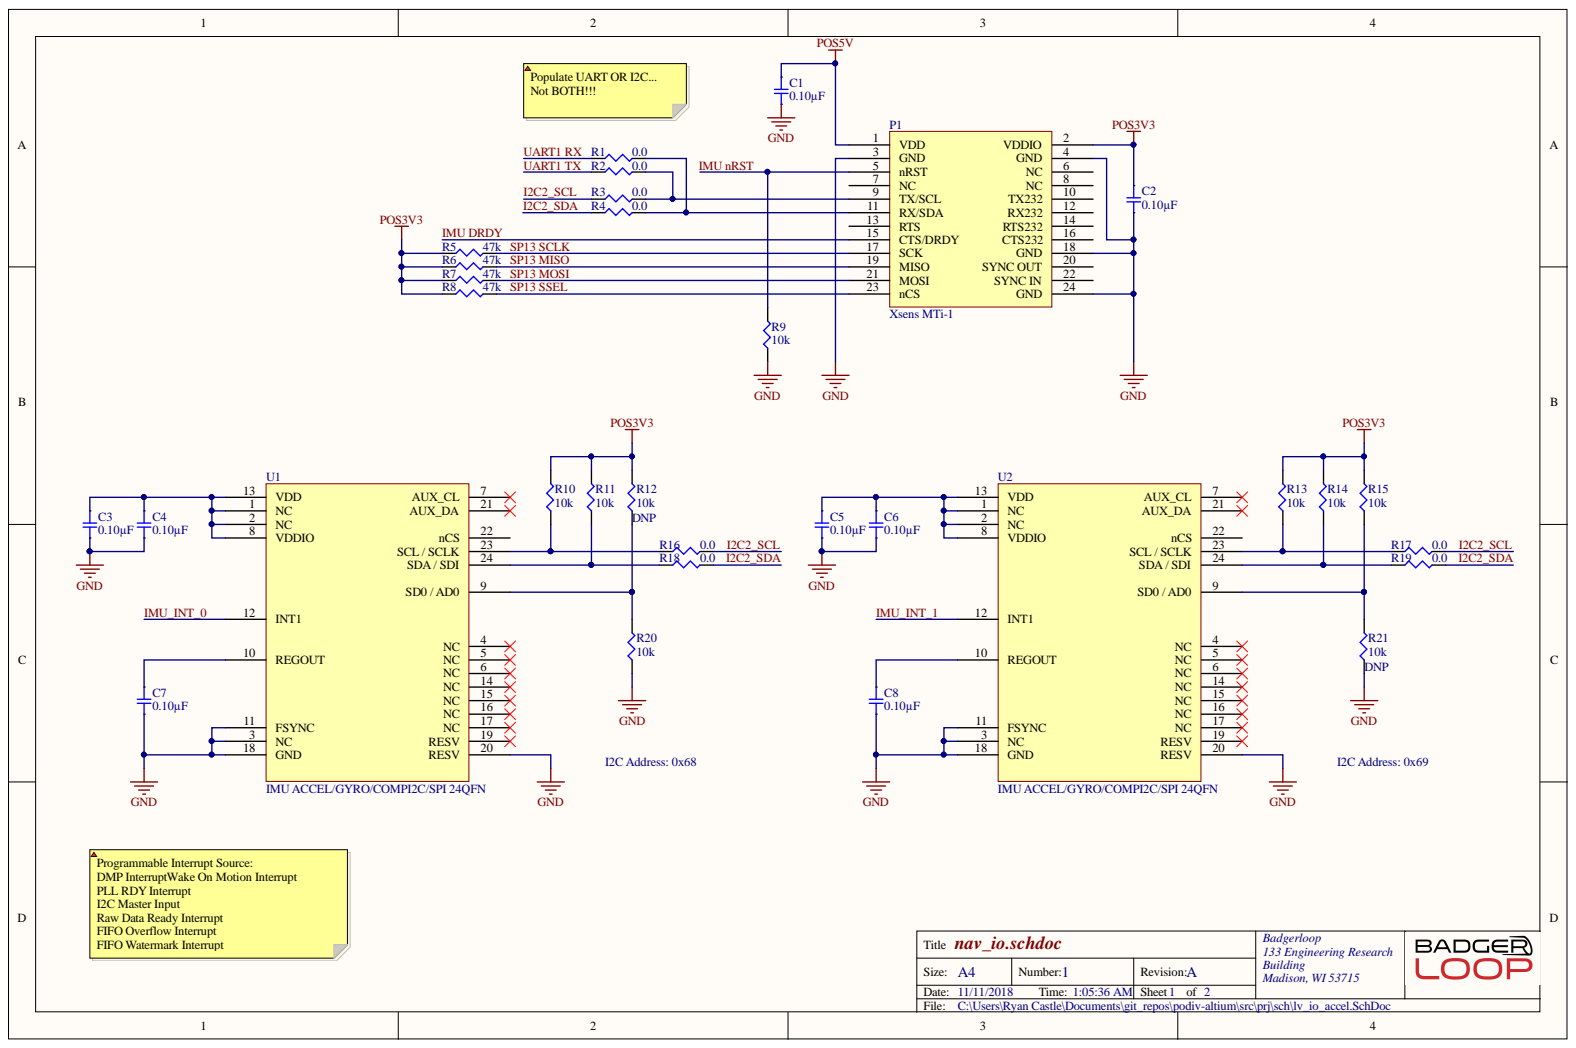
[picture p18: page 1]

IMU ACCEL/GYRO/COMPI2C/SPI 24QFN

Programmable Interrupt Source:
DMP InterruptWake On Motion Interrupt
PLL RDY Interrupt
I2C Master Input
Raw Data Ready Interrupt
FIFO Overflow Interrupt
FIFO Watermark Interrupt

Title nav_io.schdoc | Badgerloop 133 Engineering Research Building Madison, WI 53715

Size: A4 | Number: 1 | Revision: A

Date: 11/11/2018 Time: 1:05:36 AM | | Sheet 1 of 2
File: C:\Users\Ryan Castle\Documents\git_repos\podiv-altium\src\prj\sch\lv_io_accel.SchDoc

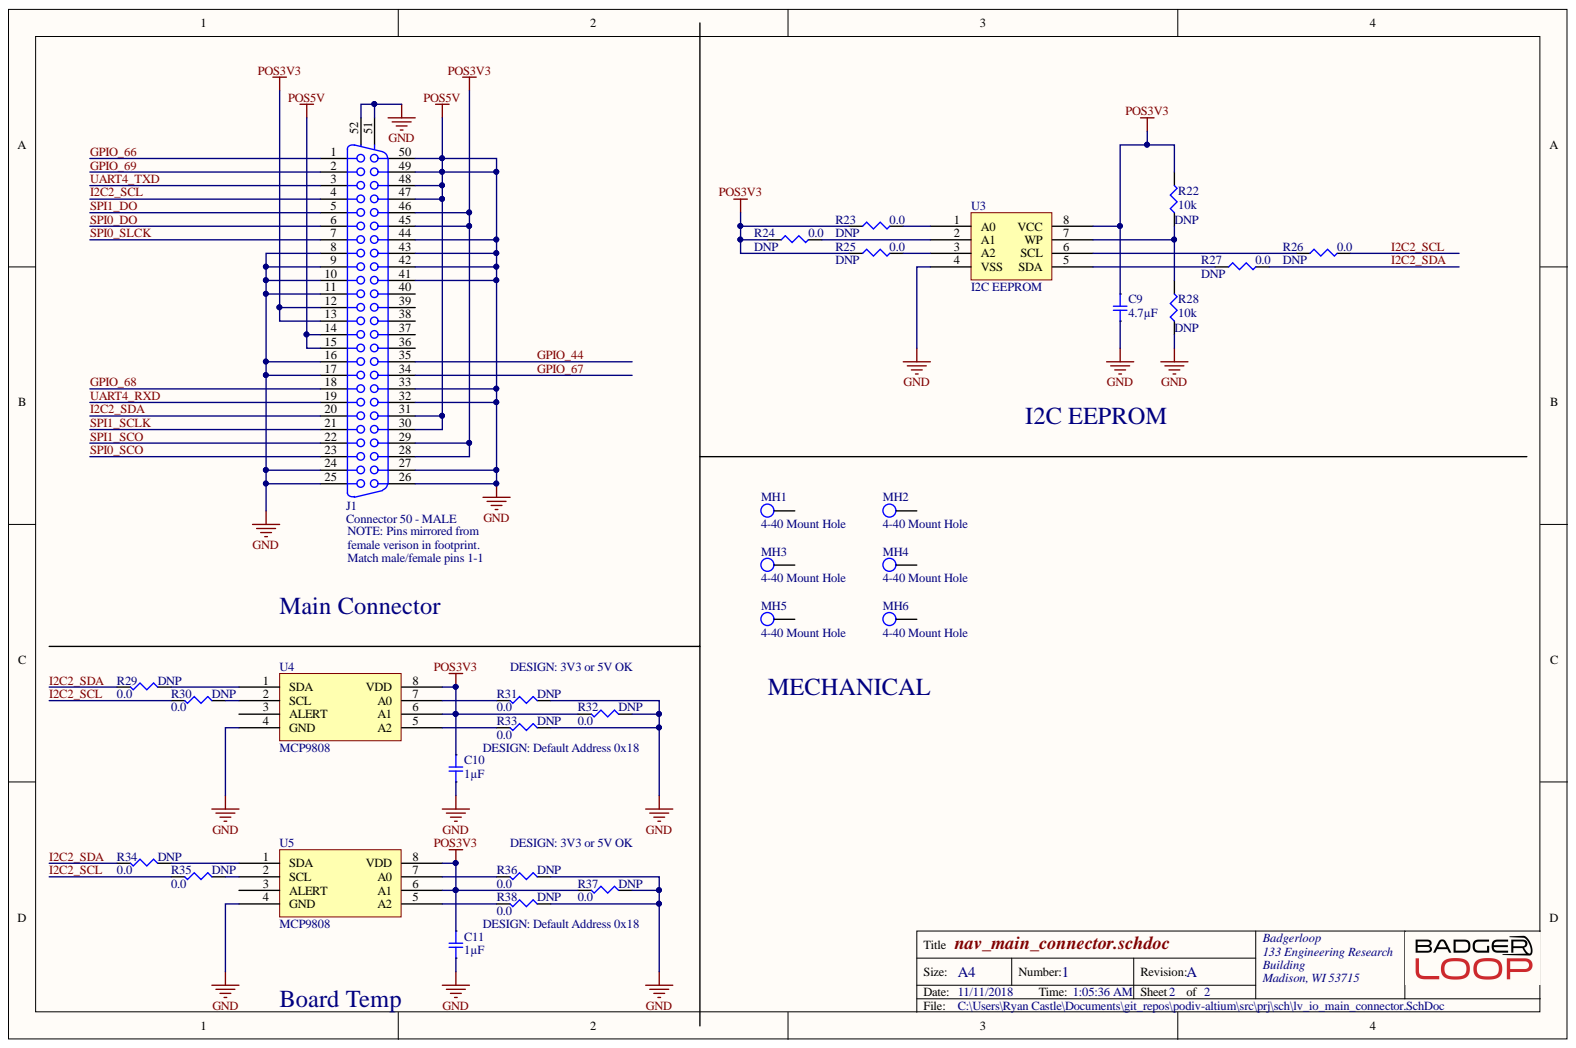
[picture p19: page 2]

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
Connector 50 - MALE
NOTE: Pins mirrored from
female verison in footprint.
Match male/female pins 1-1

Title nav_main_connector.schdoc | Badgerloop 133 Engineering Research Building Madison, WI 53715

Size: A4 | Number: 1 | Revision: A

C:\Users\Ryan Castle\Documents\git_repos\podiv-altium\src\prj\sch\lv_io_main_connector.SchDoc

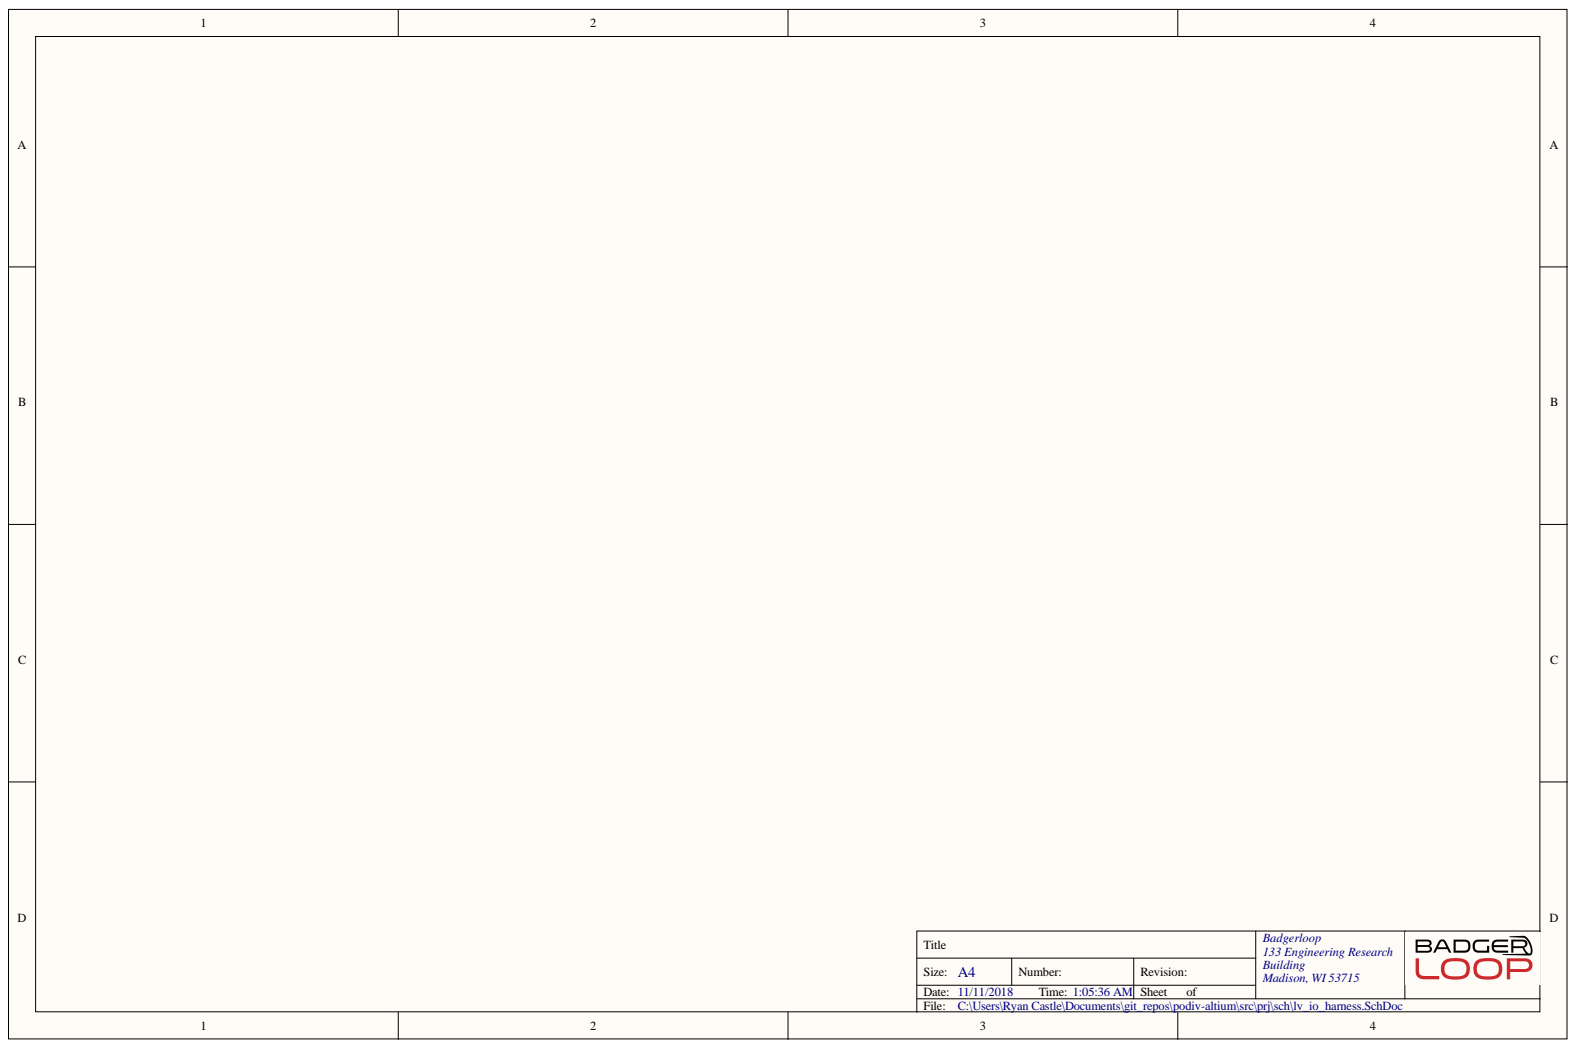
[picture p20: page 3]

Title | Badgerloop 133 Engineering Research Building Madison, WI 53715

Size: A4 | Number: | Revision:

Date: 11/11/2018 Time: 1:05:36 AM | | Sheet of
File: C:\Users\Ryan Castle\Documents\git_repos\podiv-altium\src\prj\sch\lv_io_harness.SchDoc


NOTE: Adjust sensitivity on
retroreflector with the sensor's
potentiometer

Estimated distance from sensor to
tube wall ~<1 m

During initial brinup, verify orange
light on sensor corresponds with PCB
LED

QMIC-0N-0A Photoelectric / Retroreflective Sensor (https://www.automationdirect.com/adc/shopping/catalog/sensors_-z-_encoders/photoelectric_sensors/dc_rectangular/retroreflective_(qm-z-cx-z-fe_series)/qmic-0n-0a)

Title | Badgerloop 133 Engineering Research Building Madison, WI 53715

Size: A4 | Number: | Revision:

Date: 11/11/2018 Time: 1:05:36 AM | | Sheet of
File: C:\Users\Ryan Castle\Documents\git_repos\podiv-altium\src\prj\sch\lv_io_retro.SchDoc


Title | Badgerloop 133 Engineering Research Building Madison, WI 53715

Size: A4 | Number: | Revision:

Date: 11/11/2018 Time: 1:05:37 AM | | Sheet of
File: C:\Users\Ryan Castle\Documents\git_repos\podiv-altium\src\prj\sch\lv_io_top_level.SchDoc




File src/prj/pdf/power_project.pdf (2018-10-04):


LTC8650S_VCC | LTC8650S_VCC

Design: Pgood pulled to GND until
Vout is within ±7.5% V programmed

Title power_PWR.SchDoc | Badgerloop 133 Engineering Research Building Madison, WI 53715

Size: A4 | Number: 1 | Revision: A

Date: 10/2/2018 Time: 7:46:09 PM | | Sheet 1 of 2
File: C:\Users\Ryan Castle\Documents\git_repos\podiv-altium\src\prj\sch\power_PWR.schdoc


VBUS --> 5V Design: Soft-Start Ti
VBUS --> 3V

Badgerloop 133 Engine ering Researc h Building Madison, WI 53715

A 4 | Numbe r : | R evision: A

D ate : 10/2/2018 Time : 7:46:09 P M | | She e t 1 of 2
File : C:\Use rs\Ryan C astle\Documents\git_r epos\podiv-altium\sr c\prj\sch\pow e r_CTL.schdoc


PCB: Kelvin Connection back to U4

REF2 3

Title nav_main_connector.schdoc | Badgerloop 133 Engineering Research Building Madison, WI 53715

Size: A4 | Number: 1 | Revision: A

Date: 10/2/2018 Time: 7:46:09 PM | | Sheet 2 of 2
File: C:\Users\Ryan Castle\Documents\git_repos\podiv-altium\src\prj\sch\power_main_connector.SchDoc


-30 T O 0V 0 to 6V 6 T O 15V 15 T O 30V | REVER SE P R OTECTED U V P R OTECTED GATE O N O V P R OTECTED

power_PR OTE CTIO N.SchDoc | Badgerloop 133 Engine ering Researc h Building Madison, WI 53715

A 4 | Numbe r : | R evision:

D ate : 10/2/2018 Time : 7:46:09 P M | | She e t of
File : C:\Use rs\Ryan C astle\Documents\git_r epos\podiv-altium\sr c\prj\sch\pow e r_P R OTECTI O N | . S chDoc












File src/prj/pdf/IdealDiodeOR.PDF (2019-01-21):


Size: A 4 | N umber: | Rev i s i o n :
Date: 1 / 2 0 / 2 0 1 9 T ime: 9 : 1 7 : 5 6 PM | | Sheet o f


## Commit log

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2018-08-25 More project setup testing
    [ic.PcbLib]
2018-08-31 Added Navigation Board, sheets to processor board. Renamed files
    [nav_io.PrjPCB, nav_io.SchDoc, nav_main_connector.SchDoc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]
2018-09-02 added bloop logo to schematic documents
    [nav_io.PrjPCB, nav_io.SchDoc, nav_main_connector.SchDoc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]
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2018-09-04 organized directory structure and deleted a few files
    [Sample.PrjPCB, nav_io.SchDoc, nav_io_project.PrjPCB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]
2018-09-04 initial files for precharge pcb project
    [precharge_main_connector.SchDoc, precharge_pcb.PcbDoc, precharge_project.PrjPCB]
2018-09-17 added initial resistor and capacitor libraries
    [nav_io_project.PrjPCB, precharge_project.PrjPCB, processor_main_connector.SchDoc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]
2018-09-19 Initial commit for POS5V and POS3V3 Rails
    [POS53V3.schdoc, POS5V.schdoc, processor_main_connector.SchDoc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]
2018-09-19 Initial commit for power design files
    [LT8642_1_A_Pinout.csv]
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2018-09-20 removed some extra resistors
    [processor_project.PrjPCB]
2018-09-20 basic power design work. config components
    [POS53V3.schdoc, POS5V.schdoc, processor_project.PrjPCB]
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2018-09-21 updated README and added Demo Circuit Design Files
    [DC2560A .XLS, DC2560A-3-CF.XLSX, DC2560A-3.DSN]
2018-09-23 restructured multiboard project to 3-board architecture
    [POS53V3.schdoc, power_POS3V3.schdoc, power_POS5V.schdoc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]
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2018-09-29 power project files. Initial configuration
    [power_CTL.schdoc, power_POS5V.schdoc, power_POS5V_POS3V3_CTL.schdoc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]
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2018-09-29 Added design files for LT8650S
    [DC2407A-3-CF.XLS, DC2407A-3.DSN, DC2407A-3.XLSX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]
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2018-09-30 power project commits. Added control and input protection circuitry
    [power_CTL.schdoc, power_PROTECTION.SchDoc, power_PWR.schdoc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]
2018-09-30 Added LED indicator circuits
    [power_CTL.schdoc, power_PROTECTION.SchDoc, power_PWR.schdoc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]
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2018-09-30 Initial routing / layout
    [power_PWR.schdoc, power_pcb.PcbDoc]
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2018-10-01 layout work. removed some test points
    [power_PROTECTION.SchDoc, power_main_connector.SchDoc, power_pcb.PcbDoc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]
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2018-10-01 routing and layout work. Getting there.
    [power_main_connector.SchDoc]
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2018-10-02 Layout work. Added voltage and current sensing
    [power_PROTECTION.SchDoc, power_main_connector.SchDoc]
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2018-10-03 ready for inital review
    [power_project.PrjPCB, power_project_BOM.xlsx]
2018-10-06 setup folder for snippets
    [accelerometer.SchDoc, distance_sensor.SchDoc, hv_indicator.SchDoc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]
2018-10-06 going through sample snippet project
    [Voltge_divider.SchDoc, sample_circuit.SchDoc, snippet_project.PrjPCB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]
2018-10-07 Deleted repeated snippet schematic and modified schematic to have common resistor values.
    [proximity sensor.SchDoc, sample_circuit.SchDoc]
2018-10-07 moved snippet project to bottom of dsnwrk to avoid conflicts
    [snippet_project.PrjPCB]
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2018-11-11 initial files for lv_io project
    [lv_io_accel.SchDoc, lv_io_harness.SchDoc, lv_io_main_connector.SchDoc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]
2018-11-16 fixed project structure and added pressure sensor / ADC circuit
    [lv_io_main_connector.SchDoc, lv_io_pcb.PcbDoc, lv_io_pressure.SchDoc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]
2018-11-19 finishing up schematic and solenoid placement
    [lv_io_accel.SchDoc, lv_io_analog_input.SchDoc, lv_io_harness.SchDoc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]
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2018-11-27 routing. Some schematic fixes
    [lv_io_analog_input.SchDoc, lv_io_pressure.SchDoc, lv_io_retro.SchDoc]
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2019-01-06 lv_io wrap up and BOMs
    [lv_io_BOM.xlsx, lv_io_BOM_Digikey.xlsx, lv_io_accel.SchDoc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]
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2019-01-06 directory cleanup. Moving power to a non-top level folder
    [ADIParametricSearch.csv, DC2407A-3-CF.XLS, DC2407A-3.DSN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]
2019-01-06 removed references to .temp libraries
    [lv_io_accel.SchDoc, lv_io_main_connector.SchDoc, lv_io_project.PrjPCB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]
2019-01-21 IdealDiodeOR project release RevA (Not released to Fab)
    [IdealDiodeOR.PrjPCB, IdealDiodeORBOM.xlsx, IdealDiodeOR_BOM_RevA.xlsx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]
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2019-01-22 LV_IO Project Initial Release (Not released to Fab)
    [lv_io_pcb.GBL, lv_io_pcb.GTL, lv_io_pcb.GTO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]
2019-01-28 Initial Relase for HV_Breakout_Board
    [breakout_board_BOM.xls, breakout_board_project.PrjPCB, hv_breakout.PcbDoc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]
2019-01-28 Added hv_breakout STEP file
    [hv_breakout.step]
2019-01-29 Moved breakout board silkscreen to opposite side, ready for release
    [hv_breakout.PcbDoc, hv_breakout.step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]
2019-01-29 adjusted MH footprint to allow for M2 Screws. Affecting all PCBs
    [hv_breakout.PcbDoc, idealdiodeOR.PcbDoc]
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2019-01-29 re-exported gerbers with M2 screws
    [hv_breakout_Gerbers.GBL, hv_breakout_Gerbers.GBO, hv_breakout_Gerbers.GBP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]
2019-02-05 power project initial release
    [power_pcb.GBL, power_pcb.GBO, power_pcb.GBP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]
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2019-02-11 Reformatting STEP outputs into ZIP
    [hv_breakout.step]
2019-02-11 Bringup documentation for First 3 PCBs
    [hv_breakout_tracking.csv, ideal_diode_tracking.csv, processor.csv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]
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2019-03-12 power board BOM added
    [power_project_BOM.xlsx]
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2019-03-23 directory restructure. removed board bringup folder. created resources folder
    [box_pinout.csv, hv_breakout_tracking.csv, ideal_diode_tracking.csv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]
2019-03-24 REV B changes fixing processor board issues
    [Processor_REVB_BOM_DIGIKEY.xlsx, hv_io.PrjPCB, processor_beaglebone.SchDoc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]
2019-04-02 first and likely last commit of all PODIII Altium files. Reference Only
    [BMS_Switches.SchDoc, CCP_Control_Panel_IO.SchDoc, CCP_I2C.SchDoc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]
2019-04-02 Adding PodIII Altium repo to resources folder. Reference only
    [BMS_Switches.SchDoc, CCP_Control_Panel_IO.SchDoc, CCP_I2C.SchDoc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]
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
